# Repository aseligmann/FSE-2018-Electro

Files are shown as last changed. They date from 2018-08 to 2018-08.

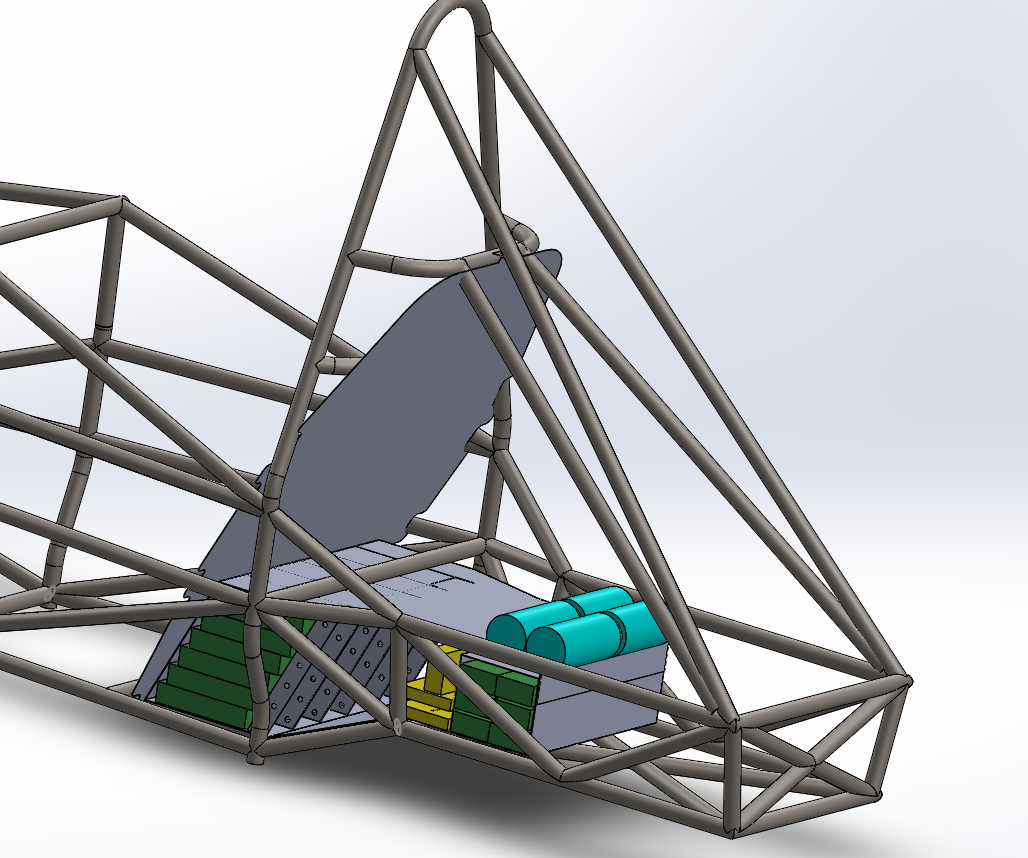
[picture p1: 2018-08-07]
Groups/Battery/Container Design/accumulator position.PNG

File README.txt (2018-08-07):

This archive contains documentation of the most electrical system in Evvee made by Vermilion Racing to participate in the Formula Student UK competition at Silverstone in 2018.
Contents are up to date as of 30/7-2018, unless otherwise noted.

Folder Structure:
	Datasheets
		Datasheets for relevant components and devices used.

	Groups
		Contains description of the work done by each of the electrical subgroups for the 2018 Formula Student race car developed by Vermilion Racing at DTU.
		See groups MasterOS and BMS for most subsystems (BSPD, TSAL etc.).

	Ongoing Sponsorships
		Description of sponsorship deals relevant to the electrical subdepartment.

	Other
		Contains misc. documents which might not be relevant for the future, but can be used as a reference.

	Rules
		Contains the rules for both Formula Student 2018 and FSUK specific rules and guidelines.

	Submitted Documents
		Contains documents relevant for the electrical subdepartment which have been submitted for the FSUK 2018 competition.

Notes:
Autodesk EAGLE has been used for schematics and technical drawings.
Currently the work done by Dominik Mariusz Maszczyk <s163601@student.dtu.dk> is not included. This includes CAN communication, electrical differential and more.

Contact:
Albert Seligmann
Head of Electrical
Vermilion Racing
T: +45 30 30 37 36
E: s163906@student.dtu.dk

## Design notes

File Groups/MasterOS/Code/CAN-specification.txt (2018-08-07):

Pedal/steering wheel position
	Sends signals:
		Normal operation (ID 110, 3 bytes)
			1 byte brake pedal position
			1 byte accelerator position
			1 byte steering wheel position
		Error (ID 10, 2 byte)
			Bit  0: Brake measurement mismatch
			Bit  1: Accelerator measurement mismatch
			Bit  2: Brake overtravel
			Bit  3: Brake undertravel
			Bit  4: Accelerator overtravel
			Bit  5: Accelerator undertravel
			Bit  6: Brake measurement connection failure
			Bit  7: Accelerator measurement connection failure
			Bit  8: Brake pedal short circuit
			Bit  9: Accelerator short circuit
			Bit 10: Steering sensor connection failure
			Bit 11: Steering sensor overtravel
			Bit 12: Steering sensor undertravel
			Bit 13: Steering sensor short circuit

	Receives signals from ID 120:
		Calibration

Audiovisual signaling
	Sends no signals.

	Receives signals from ID 110:
		Normal operation

	Receives signals from ID 10:
		Error

	Receives signals from ID 220:
		Ready to drive

Cooling control
	Sends signals:
		Normal operation (ID 710, 1 byte)
			1 byte cooling control signal

	Receives signals from ID 780:
		Motor status signal

Master
	Sends signals:
		Calibration (ID 120, no message)

		Ready to drive (ID 220, no message)

		Motor status signal (ID 780, 2 byte)
			1 byte motor power
			1 byte motor temperature

	Receives signals from ID 10:
		Error

	Receives signals from ID 110:
		Normal operation

	Receives signals from ID 710:
		Normal operation    ///not anymore

	Receives signals from ID 810:
		Normal operation

	Receives signals from ID 4:
		Error

GLVS BMS
	Sends signals:
		Normal operation (ID 810, 9 byte)
			1 byte temperature sensor 1
			1 byte temperature sensor 2
			1 byte cell1 voltage
			1 byte cell2 voltage
			1 byte cell3 voltage
			1 byte cell4 voltage
			1 byte cell5 voltage
			1 byte cell6 voltage
		Error (ID 4, 9 byte)
			1 byte temperature sensor 1
			1 byte temperature sensor 2
			1 byte cell1 voltage
			1 byte cell2 voltage
			1 byte cell3 voltage
			1 byte cell4 voltage
			1 byte cell5 voltage
			1 byte cell6 voltage

Dashboard
	Receives signals from ID 20, 3 bytes:
		byte 1 (led status)
			Bit  0: Tractive System Indicator
			Bit  1: RTD Indicator
			Bit  2: AMS error Indicator
			Bit  3: IMD error Indicator
		byte 2: Low Voltage Indicator
		Byte 2: High Voltage Indicator

	Sends signals on ID 22, 1 bytes:
		Bit  0: Tractive system activation
		Bit  1: Ready to drive

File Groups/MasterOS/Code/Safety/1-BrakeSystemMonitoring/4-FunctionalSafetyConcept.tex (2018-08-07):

\section{Functional safety concept}
% Reference: DS/ISO 26262-3 section 8
%
% Pre-requisites:
%    - Item definition
%    - Hazard analysis and risk assessment
%    - Safety goals
% 
% Reference: DS/ISO 26262-3 section 8.3.1

\subsection{Pre-existing information}
% The following information can be considered:
%    - Prior architectural assumptions (non-safety related)
%
% Reference: DS/ISO 26262-3 section 8.3.2
The brake monitoring system architecturally consists of the following parts:
\begin{itemize}
\item Brake pedal position sensor
\item Computing system
\item Brake light.
\end{itemize}

\subsection{Derivation of functional safety requirements}
% Functional safety requirements must be specified following DS/ISO 26262-8 section 6.
%
% A functional safety requirement specifies the safety measures and mechanisms that are
% required to comply with the safety goals.
% The functional safety concept is the set of functional safety requirements and the
% architectural elements of the item that they are assigned to.
% The functional safety concept is concerned with:
%    - Fault detection and failure mitigation
%    - Transitioning to a safe state after faults have been detected
%    - Fault tolerance mechanisms, where faults do not lead directly to violation of
%      the safety goals and a safe state is maintained (possibly with degradation)
%    - Fault detection and driver warning to reduce risk exposure time
%    - Arbitration logic to select "worst" fault in case of several simultaneous control
%      requests by different functions
%
% The functional safety requirements are derived from the safety goals and safe states,
% taking into account any prior architectural assumptions.
% One functional safety requirement can be valid for several safety goals.
%
% If a safe state cannot be reached by transition within an acceptable time interval,
% an emergency operation must be specified (e.g. if immediately switching off a system
% would not help, it might help to have it function in a degraded state).
%
% If assumptions are made about the reaction of the driver or other people at risk, the
% assumed actions must be specified in the functional safety concept and the controls
% available to the driver to do this must be specified.
%
% Required information:
%    - At least one functional safety requirement for each safety goal, specified by 
%      considering:
%        - Operating modes of the item
%        - Time interval of fault tolerance, i.e. how long before hazardous event occurs
%        - Safe states of the item (from safety goals)
%        - Emergency operation interval
%        - Functional redundancies (fault tolerance)
%
% Reference: DS/ISO 26262-3 section 8.4.2
\begin{description}
\item [1-FR1-D] To prevent a violation of 1-SG1-D and 1-SG2-D in the event of a light emitting device malfunction, two different systems, employing two different light emitting devices, shall be controlled by the brake system monitoring.
This will immediately lead to a degraded, but safe, state in case of a light emitting device malfunction.
Continuing to drive after transitioning to the degraded state is considered emergency operation, and the malfunction must be corrected as soon as possible.

\item [1-FR2-D] To prevent a violation of 1-SG2-D in the event of a brake light control system malfunction, a safe state shall be maintained by implementing the brake light control system as a normally closed system, so that the brake light will shine when no control signal is detected.
Continuing to drive while no control signal is detected is considered emergency operation, and the malfunction must be corrected as soon as possible.

\item [1-FR3-D] The brake light system and the driver can not detect whether a malfunction has occurred, so to prevent the violation of 1-SG3-D, a bystander will have to alert the driver, who must then bring the car to a stop as soon as possible.
This can be done by e.g. signalling the driver via flags.

\item [1-FR4-D] To prevent a violation of 1-SG4-D in the event of a brake pedal position sensor malfunction, two different systems, employing two different brake pedal position sensors, shall be employed by the brake system monitoring to determine the position of the brake pedal.
If the two systems disagree, the tractive system must be disabled and the driver must be alerted.

\item [1-FR5-D] To prevent a violation of 1-SG4-D in the event of a brake pedal position sensor giving an implausible measurement, the brake pedal position sensors shall be confined to a limited range of operation, and values outside of this range shall send a signal to High Voltage Control to disable the tractive system.
\end{description}

\subsection{Allocation of functional safety requirements}
% Each functional safety requirement shall be allocated to the elements of the prior
% architectural assumptions.
%
% When allocating, the ASIL is inherited from the associated safety goal.
% If several functional safety requirements are allocated to the same architectural
% element, the highest ASIL is inherited unless it can be argued that the safety
% requirements are independent in the architecture.
% 
% If an item consists of more than one system, the functional safety requirements
% for the individual systems and their interfaces shall be specified.
%
% If functional safety requirements are implemented by external measures, the safety
% requirements that are implemented shall be derived and communicated.
% Additionally, the safety requirements of the interfaces with external measures
% shall be specified.
%
% Required information:
%    - Allocation of each functional safety requirement to elements of the architecture
%    - ASIL for development of each functional safety requirement
%    - Functional safety requirements of interfaces to external measures/internal systems
%
% Reference: DS/ISO 26262-3 section 8.4.3
The brake pedal position sensor shall implement the following functional safety requirements:
\begin{itemize}
\item 1-FR4-D.
\end{itemize}
The brake light shall implement the following functional safety requirements:
\begin{itemize}
\item 1-FR1-D
\item 1-FR2-D
\end{itemize}
The team and other bystanders shall implement the following functional safety requirements:
\begin{itemize}
\item 1-FR3-D.
\end{itemize}

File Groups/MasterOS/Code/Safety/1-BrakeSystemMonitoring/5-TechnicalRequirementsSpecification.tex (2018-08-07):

\section{Technical requirements specification}
% Reference: DS/ISO 26262-4 section 6
%
% Pre-requisites:
%    - Functional safety concept
% 
% Reference: DS/ISO 26262-4 section 6.3.1

\subsection{Pre-existing information}
% The following information can be considered:
%    - Safety goals
%    - Functional concept
%    - Prior architectural assumptions
%
% Reference: DS/ISO 26262-4 section 6.3.2
The brake monitoring system architecturally consists of the following parts:
\begin{itemize}
\item Brake pedal position sensor
\item Computing system
\item Brake light.
\end{itemize}

% The technical safety requirements are a refinement of the functional safety
% requirements, taking in account the prior architectural assumptions, and
% turning the item-level functional requirements into system-level technical
% requirements.
%
% The technical safety requirements should be specified considering the following
% properties of the system:
%    - Functional safety requirements
%    - Prior architectural assumptions
%    - External interfaces, e.g. communication and user interfaces
%    - Environmental and functional constraints
%    - (Re)configuration requirements
%    - Dependencies on other systems/elements
%    - Requirements during production, operation, maintenance and repair
%
% If a system should implement functions that are not described by the technical
% safety requirements, a reference should be made to their specifqication.
%
% The technical safety requirements shall specify the response of the system to
% events that affect the achievement of safety goals, including:
%    - Detection, indication and control of faults in the system and communication
%    - Detection, indication and control of faults in external devices/systems
%    - Measures to maintain or transition to a safe state
%    - Measures to implement the warning and degradation concept
%    - Measures to prevent latent (undetected root cause, "random'') faults, e.g. self
%      tests on power up (only for ASILs C and D).
%
% Required information:
%    - Technical safety requirements for the functional safety requirement (see above)
%    - Transitions, fault tolerant time interval, emergency operation interval and
%      measures to maintain state for each safety mechanism that enables a safe state
%    - For safety requirements assigned ASILs C or D, safety mechanisms to prevent
%      latent faults
%
% References:
%    - DS/ISO 26262-4 section 6.1 -- 6.2 and 6.4.1 -- 6.4.5
%
% <<< Repeat this section for each hazardous event >>>
\subsection{1-FR1-D}
This functional safety requirement must be implemented by the brake light system.
This functional safety requirement prescribes that the brake light system must contain two different light emitting devices.

\paragraph{1-TR1-D}
The brake light must be implemented by two electrically parallel light emitting devices, so that the failure of one device does not affect the other.

\subsection{1-FR2-D}
This functional safety requirement must be implemented by the brake light system.
This functional safety requirement prescribes that the brake light control system must be a normally closed system.

\paragraph{1-TR2-D}
The brake light control system must supply power to the brake light when no control signal is detected (i.e. when the control signal is ``floating'').

\subsection{1-FR4-D}
This functional safety requirement shall be implemented by the brake pedal position sensor.
This functional safety requirement prescribes that the brake pedal position sensor shall measure the  brake pedal using two different position sensors, and that the tractive system must be disabled and the driver alerted if the sensors disagree.

\paragraph{1-TR3-D}
The brake pedal position sensor must be implemented by two different position sensors with differing transfer functions.

\paragraph{1-TR4-D}
The two position sensors mentioned in 1-TR3-D must be compared using non-programmable hardware to detect disagreements.
The comparison hardware must be adjustable to compensate for temperature and wear.

\paragraph{1-TR5-D}
If a disagreement between the two position sensors mentioned in 1-TR3-D is detected, a signal must immediately be sent to High Voltage Control to disable the tractive system.

\paragraph{1-TR6-D}
If a disagreement between the two position sensors mentioned in 1-TR3-D is detected, a designated light on the dashboard must be lit to warn the driver.

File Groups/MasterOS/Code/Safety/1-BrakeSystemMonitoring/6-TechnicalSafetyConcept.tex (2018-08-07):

\section{Technical safety concept and system design specification}
% Reference: DS/ISO 26262-4 section 7
%
% Pre-requisites:
%    - Technical safety requirements specification
% 
% Reference: DS/ISO 26262-4 section 7.3.1

\subsection{Pre-existing information}
% The following information can be considered:
%    - Prior architectural assumptions
%    - Functional concept (non-safety related)
%    - Functional safety concept
%
% Reference: DS/ISO 26262-4 section 7.3.2
The brake system monitoring consists of the following overall systems:
\begin{itemize}
\item Brake pedal position sensor
\item Computing system
\item Brake light.
\end{itemize}
\subsubsection{Brake pedal position sensor}
This system consists of the following elements:
\begin{itemize}
\item Position sensors
\item Brake system plausibility device
\item Communication
\end{itemize}

\subsubsection{Computing system}
This system consists of the following elements:
\begin{itemize}
\item Communication
\item Brake pedal overtravel detection
\item Brake position sensor disagreement detection
\end{itemize}

\subsubsection{Brake light}
This system consists of the following elements:
\begin{itemize}
\item Communication
\item Light emitting devices
\end{itemize}

% The technical safety concept is the allocation of the technical safety requirements
% to system elements that are to be implemented by the system design.
% Each element shall inherit the highest ASIL from the technical safety requirements
% that it implements.
%
% The system architectural design implements the functional safety requirements,
% technical safety requirements and non-safety-related requirements.
% When implementing the technical safety requirements, the following shall be 
% considered:
%    - The ability to verify that the system design fulfills the requirements
%    - The technical capability of the design to achieve functional safety
%    - The ability to execute tests during system integration
%    - The allocation and partitioning decisions from the technical safety concept
%
% Required information:
%    - Allocation of technical safety requirements to hardware and/or software elements
%    - Interfaces between system elements and to other systems
%    - Measures for detection, control and mitigation of random hardware failures
%    - Qualitative safety analyses on the system design to identify and eliminate
%      systematic failures and faults
%
% Reference: DS/ISO 26262-4 section 7.4.1 -- 7.4.5
% <<< Repeat this section for each system required to implement the item >>>
\subsection{Position sensors}
This system element shall implement 1-TR3-D.
Therefore, this system element is assigned ASIL D.
It is trivial to verify and test that the element fulfills 1-TR3-D, as it can be easily decided from measurements on the position sensors.

\subsection{Brake pedal overtravel detection}

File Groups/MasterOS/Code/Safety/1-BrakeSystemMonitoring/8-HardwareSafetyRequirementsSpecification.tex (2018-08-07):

\section{Hardware safety requirements specification}
% Reference: DS/ISO 26262-5 section 6.1 -- 6.4.8
%
% Pre-requisites:
%    - Technical safety concept
%    - System design specification
%
% Reference: DS/ISO 26262-5 section 6.3.1

\subsection{Pre-existing information}
% The following information can be considered:
%    - Software safety requirements specification
%
% Reference: DS/ISO 26262-5 section 6.3.2

\subsection{TECHNICAL SAFETY REQUIREMENT NAME}
% Hardware safety requirements shall be derived from each technical safety requirement
% allocated to hardware.
% If a technical safety requirement is allocated to both hardware and software, it should
% be partitioned to yield hardware only safety requirements.
%
% The hardware safety requirements shall include each hardware requirement that relates
% to safety, including:
%    - Safety mechanisms to control internal hardware failures, e.g. a watchdog timer
%    - Safety mechanisms to ensure the element is tolerant to external failures, e.g.
%      an open circuit input to a processor
%    - Safety mechanisms to comply with the safety requirements of other elements
%    - Safety mechanisms to detect and signal internal or external failures
%    - Hardware safety requirements not specifying safety mechanisms, e.g. avoidance
%      of unstable output, requirements for cables and connectors, etc.
%    - Fault tolerant time interval for safety mechanisms from technical safety requirements
%
% The criteria for verification of the hardware design shall be specified, including:
%    - Temperature, vibration, EMI, and other environmental conditions
%    - Supply voltage and other specific operational environment conditions
%    - Component specific requirements
%
% Required information:
%    - Hardware safety requirements for the technical safety requirement
%
% Reference: DS/ISO 26262-5 section 6.4.1 -- 6.4.8
% <<< Repeat this section for each technical safety requirement assigned to hardware >>>

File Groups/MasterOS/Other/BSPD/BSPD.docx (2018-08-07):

# BSPD

Opamps should not get any input voltages higher than Vdd-1.5 which in our case is 10.5V of the 12V.

To secure that the logic gates don’t give out Vdd to the op amps the logic gates Vdd is regulated down to 10.47V.

Break pedals should only operate from 1 to 10V under normal conditions.

Every input and output goes through a fuse to protect the circuit from over current. Every input is checking for short circuit and open circuit with opamps. When an open circuit happens the opamp side is pulled down to ground and thus simulating a short circuit to ground. 0.64V is considered short circuit to ground, 10.43V is considered short circuit for the break pedals. Lem sensor goes from ~0.63V to 3.84V under normal operation. Everything above or below this value is considered short circuit or too high current draw from the battery thus shutting down.

Under normal operation both break pedal sensors will be checked. If one of them goes above a certain voltage e.g. R20/(R20+R1) while current draw is above 40A (2.55V from the lem sensor) The vehicle will shutdown.

To ensure that abnormal behavior is priorities, every short, open and over current, triggers the charge circuit directly. This is ensured by the logic in the circuit. If a error is present for roughly 300ms the vehicle will shutdown. If no error is present the charge circuit discharges through a low resistor and a mosfet.

The output of the circuit goes to LOW when a error is present and thus closes a relay on the shutdown board. So if the output fuse breaks the shutdown circuit will be activated.

R14, R15, R20 and R1 can be changed to change the position where the break pedal sensor triggers the opamp.

R8 and R9, and, R7 and C1, can be used to change the charge time.

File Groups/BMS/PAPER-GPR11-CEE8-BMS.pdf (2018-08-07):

## Battery Safety System for Electric Racing Vehicle

Joakim Vollertzen, s163947 Søren Simonsen, 163907

Department of Electrical Engineering, Technical University of Denmark Course 31015 Introductory project - Electrotechnology

Abstract - The Vermillion racing team is a newly made project on DTU and is working on building an electric race car. The car will be participating the Formula Student Electric competition. More than 100 teams from different universeties will be competing on who can build the best race car. This project is mainly focused on implementing a battery system in the car based on Lithium Polymer technology. When working on batteries, safety is the top priority. The main systems will consist of a BMS to monitor and manage the battery packs. This will be a bought solution, but there is still a lot of research about the batteries required. A power systems board will have to be designed and made. This system will make sure that the battery box will be isolated from the rest of the system in case of a fault or emergency. A seperate system will also be designed and made to indicate the activity status of the battery box. This will have to detect both the outside voltage of the battery pack and the physical state of the relays. This project will be in collaboration with other department spread out on the mechanical and electrical department. All these departments will be under the Vermillion Racing team, and the ultimate goal is to compete and win in the competition.

I. INTRODUCTION

This project is part of a larger project, which goal is to design and build an electric racecar. The car will be entirely designed and build by DTU students and will compete in the Formula Student Electric (FSE) competition at the Silverstone track in England. this project is a part of the Vermillion racing team, which team consist of about 50 DTU students. The Formula Student is a Blue Dot project, and is expected to continue each year from now on. This means that the parts designed and produced in this project will either be optimized or used as inspiration in next years competetion.
This project is focused on the development of a Battery safety system. This system is mainly responsible for monitoring the battery system and disconnecting the battery from the rest of the high voltage system (tractive system) in case a fault is detected in the car. This system will include a Battery Management system (BMS), a Tractive System Active Light (TSAL), and a power systems board.
The battery will be isolated from the rest of the system through a two Accumulator Isolation Relays (AIR). The power systems board will make sure any of the safety systems and shutdown buttons is able to disconnect the relays in case of a fault.
The car will have a large battery container consisting of several lithium-polymer batteries. These kind of batteries contain a large amount of energy that they can discharge very fast. Because of that, it’s very important to handle the batteries in the right way to make sure the car and the people close to it are safe.
Working with the batteries is not easy, and a lot of safety precautions have to be made. It’s important to know exactly which state the batteries are in. If the batteries are not in use, or if an emergency should arise, it’s also important to be able to disconnect the battery box from the rest of the system. There are three main problems which arise when working on a battery system:
1. How can we monitor and manage the battery within safe conditions?
2. How can we make sure that the battery is only connected to the tractive system when it’s safe and desired?
3. How can we indicate the activity status of the tractive system?

II. "PROBLEMS AND RISKS"

Lithium Polymer (LiPo) batteries have a large advantage over other battery technologies as they have a high energy density and discharge rate. This makes it possible for the car to drive further and accelerate faster. The disadvantage is that they are more complicated to operate, and they are more dangerous if a fault should occur.
Different problems can arise when working with LiPo batteries. The battery packs consist of smaller cells, and if their voltage is too low or high, or if the voltages of the cells are not balanced, the battery can destroy itself and in the worst case ignite or explode. This kind of battery have a very high discharge rate and high capacity, if a load draws too much power or if the battery is shorted, it can overheat and ignite or explode. The battery in the car is made out of several smaller packs packed into a box. If the battery box is not operated safely, there is a risk of fire, explosion and/or electrocution. The safety of the battery system is therefore the top priority for this project.
The battery packs will be mounted in a large battery box. To monitor and regulate the battery box, a BMS must be implemented in it. The BMS will constantly measure the voltage of all the cells and make sure they are at a safe level. The total power output of the battery box will also have to be measured to make sure that the connected load won’t draw more current than the batteries can safely provide. Several temperature sensors will be mounted inside the battery box to make sure the batteries are not overheating. To charge the battery, a charger made for the battery setup is necessary. The charger will communicate with the BMS over a CAN bus so the cells can be balanced correctly and so the battery won’t get overcharged.
The battery box will be connected to a pair of motor controllers which controls the motors and decides how much power is used by each motor. These motor controllers have a high capacitance. Because of the high discharge rate of the batteries, a pre-charge system must be implemented to limit the in-rush current to the motor controllers. Otherwise, the relays may weld shut and it wont be possible to open them again. The pre-charge system will charge the motor controllers capacitor banks via a power resistor to limit the current. When the outside system voltage reach at least 90% of the full battery voltage, it is safe to close the main relays. When the battery box is disconnected again after use, the capacitor bank in the motor controllers will still be charged. Therefore, a discharge system will have to be made. The discharge system will dissipate the remaining energy in the motor controllers through an array of power resistors. This should happen in less than 5 seconds to make sure the car is safe after the battery box has been disconnected.
Beside potential battery faults, many other faults and dangers can occur in a race car. These faults can be either electrical errors or accidents. If these faults occur, it can be dangerous to the driver and it can destroy the electrical system. It is therefore important that the battery box is quickly disconnected from the tractive system if a fault or accident should happen.
Some of the faults that can occur are isolation errors, battery errors, crashing and brake errors. The isolation error can be detected by using a device which can measure the low voltage system and the battery box and trigger if an isolation error has occured. We need to make sure that the battery box will be disconnected from the tractive system in case the car is in a crash to limit the risk of short circuits and electrocution. To ensure the car is used correctly, the car should only start when the driver and the team is ready to drive the car. It will therefore be needed to have a master switch which will be used to turn on the tractive system. To make it possible to work on the low voltage system without having to remove the low voltage batteries, a master switch to connect the low voltage battery to the low voltage system is needed. Several emergency shutdown buttons will also be mounted on the inside and outside of the car to make sure any person can disconnect the battery in case of an accident. Because the electrical system will be used in a car, there is a risk of water damage and the car shaking. To protect the electrical components in the car, all components must either be water proof or placed in a water proof container. They will also be mounted securely to the car so they wont shake out of place To indicate that the battery box is completely disabled and all the relays are open, a Tractive System Active Light (TSAL) must be implemented. The TSAL itself can’t affect the electrical system, and is only an indication of the battery box status. Even though the battery box have several safety systems, it’s important to have a seperate system to monitor and indicate the activity status of it. This ensures that a person can see clearly if the car and battery box itself is safe to be around. Because the TSAL is isolated from the rest of the system, a fault is unlikely to affect the function of the indicator.
To ensure that the TSAL always indicate the status of the battery box, it will have to measure the physical state of the main relays (AIRs) and the outside system voltage present on the battery box terminals. It will be measured by nonprogrammable logic which is only powered by the battery. If any of the relays are physically closed or if the outside system voltage exceed 50 V, the TSAL must blink red. If all relays are open and the outside voltage is below 50 V, the TSAL will switch to a constant green ligth.

III. "RESEARCH AND DEVELOPMENT"

The problems and risk mentioned in last section have to be solved so that the car is both safe for use but also compliant with the FSE rules. This means that our solution will be heavely influenced by the rules so that the car can compete in the competetion without any penalty points.
All the faults described in the previous section are used to decide when the car is safe to drive. All these faults will be detected by seperate systems in the car, and when these faults are detected, the AIRs will open and isolate the battery. To make sure that the AIR’s are only activated when desired, the current activating the AIR’s must be directly supplied by the low voltage system and flow directy through the relays, switches and buttons that activate them. This is done so each part of the safety system can directly stop the current from reaching the AIR’s. The safety system will be centered around a power systems board. This board will be a PCB and is where the relays will be placed. These relays will then be closed by their respective safety systems. All these relays, buttons and switches are a part of the low voltage system and use 24V. The power systems board will also have the relays necessary to control the pre-charge and discharge phase along with relays to control the individual AIRs. This is mainly used by the BMS. As the pre-charge and discharge systems are connected directly to the tractive system, they are galvanically isolated from the low voltage system present on the power systems board.

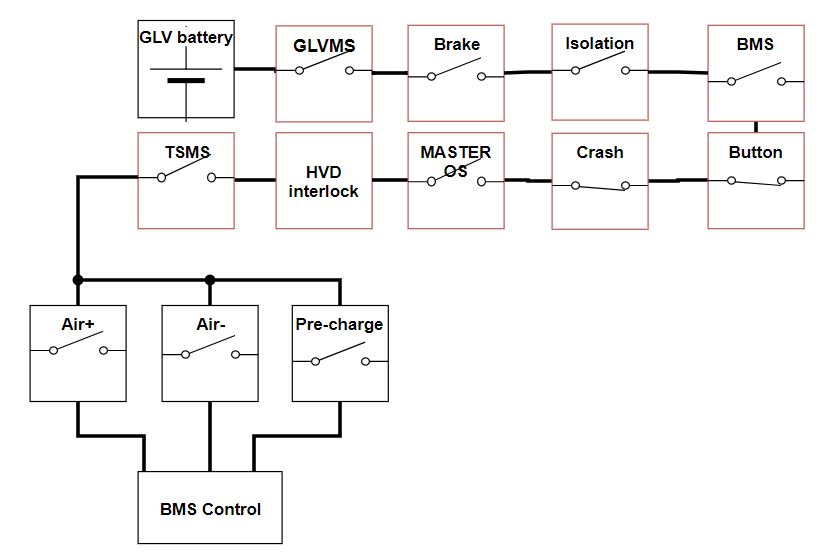
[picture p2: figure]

Fig. 1. Simple block diagram of safety system

Figure 1 shows a blockdiagram of the safety system responsible for opening and controlling the AIR’s. The first block after the low voltage battery is the Ground Low Voltage Master Switch (GLVMS). This switch supplies power to all the systems in the car which use 24V, and is the first swich needed to be turned on in order to start the car. This is a master switch, and it is important that it will not be turned when it is not needed. When the switch is turned off, the handle can be removed and the switch can be locked and tagged. The brake errors consists of two subsystems. The break system plausibility device make sure that the battery is disconnected if the car is accelerating and braking at the same time. This means that the driver can always stop the car if the accelerator is stuck due to either software or hardware fault. The break overtravel switch will disconnect the battery if the break pedal is pushed all the way down. This can happen if the brake fluid is leaking. These are not systems designed in this project, but they will have a relay each on the power systems board.
The isolation error is detected by a BENDER ISOMETER® IR155-3203/IR155-3204. This part is required to be used by the competetion, and makes sure that the battery is always isolated from the low voltage system and the car chassis ground. The relay will have to be latched so the battery is disconnected until the fault is inspected and fixed.
The BMS relay in the safety system is latched in the same way that the iosolation is. Both the Isolation and the BMS need an indicator light on the dashboard of the car, so the driver and the team know where the fault lies. This light needs to be on until the relay on the power systems board has been manually reset. These indicators will be controlled directly by the cars master controller.
Three emergency shutdown buttons will be located on the car. One in the cockpit and one on each side of the car. According to the rules of FSE, these buttons must either be push-pull or push-rotate, and all three buttons must be able to disconnect the current flow to the AIR’s directly.
The crash sensor is a 360 degrees sensor which detects impact load. When an impact load between 6g and 11g is detected, it opens the safety system. The crash sensor can be reset by pushing a button on the device.
The master controller will also have a relay on the power systems board, and in therefore able to connect and disconnect the battery when starting and stopping the car. It is therefore also able to disconnect the battery in case of a fault.
The next box in figure 1 is the High Voltage Disconnect. It works by opening the safety system when the cable connecting the battery box and the motor controller is disconnected. This is done through a interlock.
The Tractive System Master Switch (TSMS) is the last link in the chain. This is a physical switch identical to the low voltage master switch, and is used to turn on the tractive system.
The tractive system can be activated when none of the parts of the safety system have detected a fault, all of the switches and buttons are closed and the driver has entered the ready to drive mode using the master controller. The relays controlled by the BMS are used to control the pre-charge sequence. After a engine start is requested, the master controller will request the BMS to run the pre-charge operation.
The discharge relay is controlled by the same signal going from the tractive system master switch to the AIR’s. The relay is normally closed, which means that the discharge phase will run automatically when the battery is disconnected. All signals which control whether the AIR’s are opened og closed are system critical. This means that they must be protected agains short circuit and open circuit. If a signal wire is broken, the relay it’s connected to will automatically open. If a short circuit of the signal wire is present, a fuse will blow and the relay will open. Therefore, all signals will go to a safe state if there is open circuit or short circuit.
In the beginning of the project, the battery setup was already set to a voltage between 80-120 V. The BMS was chosen to be a LiBAL N-BMS as Lithium Balance would like to sponsor it. The system is very flexible and can work with several battery configurations. Because of that, most of the work was already done with the BMS.
In 2, a simple block diagram of the battery system can be seen. The BMS consist of a master board with three slave boards connected to it. The battery systems is made of 7 battery segments in series each consisting of 6 battery packs in parallel. Each segment will have 4 temperature sensors and 4 cells which voltages are monitored by a slave module. The slave boards are able to measure the voltage of the cells and balance them through on-board resistors. The battery temperature can also be measured in several different locations using external sensors. The master board is measuring the total battery voltage along with the cell voltages and controlling the charging and balancing of the cells. Through a hall-effect current sensor, the current through the battery is measured to ensure the safety threshold is not exceeded. Using three external relays located on the power systems board, the BMS master is able to close the two AIR’s and the pre-charge relay to control the pre-charge operation safely.
The rules specified that a third of the cells must have a temperature sensor mounted at the negative pole. This was problematic for both the BMS and the battery box itself. All the temperature sensors would cause space problems in the pack because of the cables, and the BMS would not be able to monitor all the sensors without getting extra slaves for it. In collaboration with our advisor, Nenad Mijatovic, and the battery group, Albert Segilmann and Frederik Højlund, a solution was found where one sensor could measure the temperature of two cells. This made it possible to fit the whole battery system in a small closed container.
The TSAL was complicated to make because of the high safety factor and many rules. It was not allowed to measure the control signals to the main signals, and must do it by directly measuring on the relay terminals. This was to make sure the TSAL measures the right state in the event that the relays got stuck or welded shut. It was also necessary to power the TSAL with the high voltage battery and not the smaller external low voltage battery. This was to make sure the TSAL would always be powered on when the battery was connected. In 3, a simple block diagram of the TSAL can be seen.

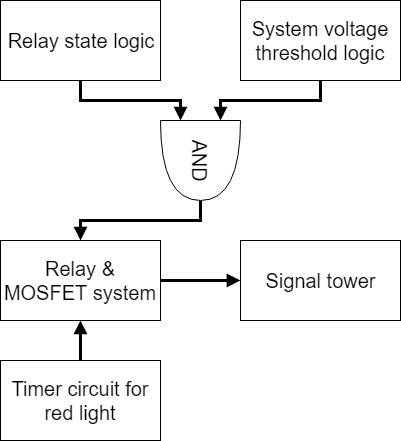
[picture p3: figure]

Fig. 3. Simple block diagram of Tractive System Active Light (TSAL)

To make sure the system will not indicate a safe state if an unknown input occur or if the trigger circuit breaks, the default state of the circuit is set to indicate an active battery. This is done via switch relays which will have the normal position blink the red light. Two independent circuits will have to both indicate a safe state, represented as the AND-gate, for the light to switch green and indicate a deactivated battery. In reality, two transistors and a relay will be in series acting like an AND-gate.
The Relay state logic will determine the state of the two main relays through a resistor. The output of the resistor network will be compared to a reference signal via two op-amps. The measured signal and reference signal is both referenced to the supply voltage, thus making it possible to work with the large range of supply voltages which occur depending on the battery charge level. Each op-amp will trigger a transistor, and if both op-amps are triggered, both relays will be open and indicate a safe state.
The system voltage threshold logic will independently measure the voltage over the battery terminals on the outside of the battery box. If the threshold of 50V is reached, an op-amp will open a relay and indicate an unsafe state. If the circuit is below 50V or completely unpowered, which will be the case if one or both of the relays are closed, the relay will close again and indicate a safe state.
If both circuits indicate a safe state, the light will switch to a constant green via switch relays. If that is not the case, the circuit will blink the red light via the timer circuit. If the circuit lose a connection to the batteries, it would not be able to determine the relay state and battery voltage. But because it’s powered by the battery, the TSAL will be unlit, and therefore indicate an error and potential unsafe state.

IV. PRODUCTION AND TESTING

The power systems board will be a PCB. This PCB mainly consists of relays and connecotors to the varius parts of the safety system. The power systems board will have both low voltage and high voltage systems. These needs to be proberly isolated from each other, which is done by placing each system at least 20 mm from each other on the PCB. The low voltage and high voltage is placed on the same PCB to save space and make a more simple system. When the power systems board has been completed, it will be placed in a closed box with waterproof connectors.
To make sure that the power systems board works properly, the board needs to be tested. The first test is to make sure all the relays and buttons work as designed. The buttons and switches will be directly connected to the power systems board, and the signals from the active systems will be emulated with a power supply.
A Arduino will be connected to an array of relays. These relays will be connected to a variable power supply to emulate different signal voltages. The Arduino can be programmed to test the relays on the board in different state configurations. By changing the voltage on the power supply, a large range of signal voltages can be tested to make sure that the system can will still work over a larger range of input signals. This is good to know in case some of the systems can’t supply a steady signal voltage.
It is important to test all possible connections on the board with a multimeter while activating the relays. This is done to test if the board is printed and designed proberly. If this test is succesfull, it would confirm that the design of the power systems board works correctly. This test will be done using the equipment in X-lap.
The second test is a test to make sure the pre-charge and the discharge relays works properly. This will be done by connecting a capacitor to emulate the motor controller. A power supply will be connected to emulate the battery box. During the test, the temperature of the resistors will be monitored to make sure they aren’t overheating.
Before mounting the batteries in the container, the BMS and all battery-related systems must be tested and approved. The test setup will be close to the one illustrated in 2, but with a few modifications. The first tests will consist of one master and two battery packs, keeping the voltage at a minimum while still being able to configure and test the BMS functionality. If the test is successful, more batteries can be added in series until the full system voltage is reached using all three slaves. The load will be in the form of an adjustable load able to dissipate all the heat, but it will only be connected after the BMS is fully configured and working. This should be connected in combination of the main relays and power systems board to test if they can safely disconnect the battery. If anything unexpected should occur under testing, this will also be used to isolate the batteries and prevent an accident. The charger we’re using will also be testet, where it’s important to check if the CAN communication between BMS and charger is working. The BMS is also checked to see if the cells are balanced and charged to the correct voltage. If there is time en resources available, it will also be possible to tweak the PID parameters of the charging operation to keep the charging time to a minimum. But this will have to be monitored closely as a underdamped PID regulation could

overcharge the batteries.
It’s important to also test the batteries in combination with the rest of the system. The relays and power systems board should be tested first, but the TSAL can also be tested easily when all the batteries in series is connected together to reach the full system voltage. Afterwards, the system will have to be implemented in the battery box where temperature tests are especially important. If the cooling in the box isn’t suffucient, the batteries can overheat in the closed container and ignite.
The TSAL will be made out of simple electronic components and soldered onto a PCB. The PCB will be fit in a waterproof box which is easy to install on the car later on. In the testing phase, a milled prototype PCB will be used. This is cheap to make and fast to mill if a correction have to be made.
To test the relay state logic, a 30V power supply is enough to power the logic and the light. A small relay will be used to emulate the function of the main relays. The four possible states of the two relays is tested, where it is expected for the light to stay red until both relays are open.
To test the system voltage threshold logic, a supply of 60V is required. While the two relays are open, the supply is increased until around 50V where the light is expected to trigger. This will also be tested with the other possible relay state combinations to make sure that the two circuits work together.
If both tests are successful, the circuit will have to be tested at the full 120 V to make sure the regulators work at higher voltages without overheating. At last, the TSAL will be tested with the full battery setup including the two main relays and the pre-charge relay. Afterwards, the TSAL can be implemented in the car.
V. CONCLUSION

Through this project, we have learned a lot about how to design and build a safe electrical battery system for a car. We have focused on what to do to protect and regulate the battery, and when to disconnect the battery from the rest of the cars electrical system.
A BMS system have been designed to monitor and regulate the batteries. The system have not been implemented yet due to delay in the BMS delivery, but the battery setup have been designed along with the tests required to make sure the BMS is working as expected.
A power systems board have been designed and the first prototype is close to be ready for testing. It is expected to go into testing shortly after the project is done. Based on the test, the design will be improved and in the end send to production at a professional PCB manufacturer.
The first design of the Tractive System Active Light have been tested, where it successfully measured when the outside system voltage reached a threshold of 50 V. The part of the circuit to check the physical state of the main relays did not pass the test, but a new design have been made and a new prototype is close to being made. This circuit will also be manufactured by a professional PCB manufacturer when it is fully tested and approved.
Overall, we are pleased with the progress we made throughout the project. we unfortunately didn’t implement all the systems, but we learned a lot about working on larger projects and collaborating with other departments.

ACKNOWLEDGEMENT

Thanks to Nedad for guiding and helping us during the project. Thanks to Esben and Bjarni for helping us with PowerLab introduction and access. Thanks to the Vermillion racing team for letting us be apart of this project. Thanks to the sponsors who made this project possible, especially Lithium Balance for giving us a course on how to use the BMS and thanks to Tonny from PowerLab for helping us milling PCB’s.

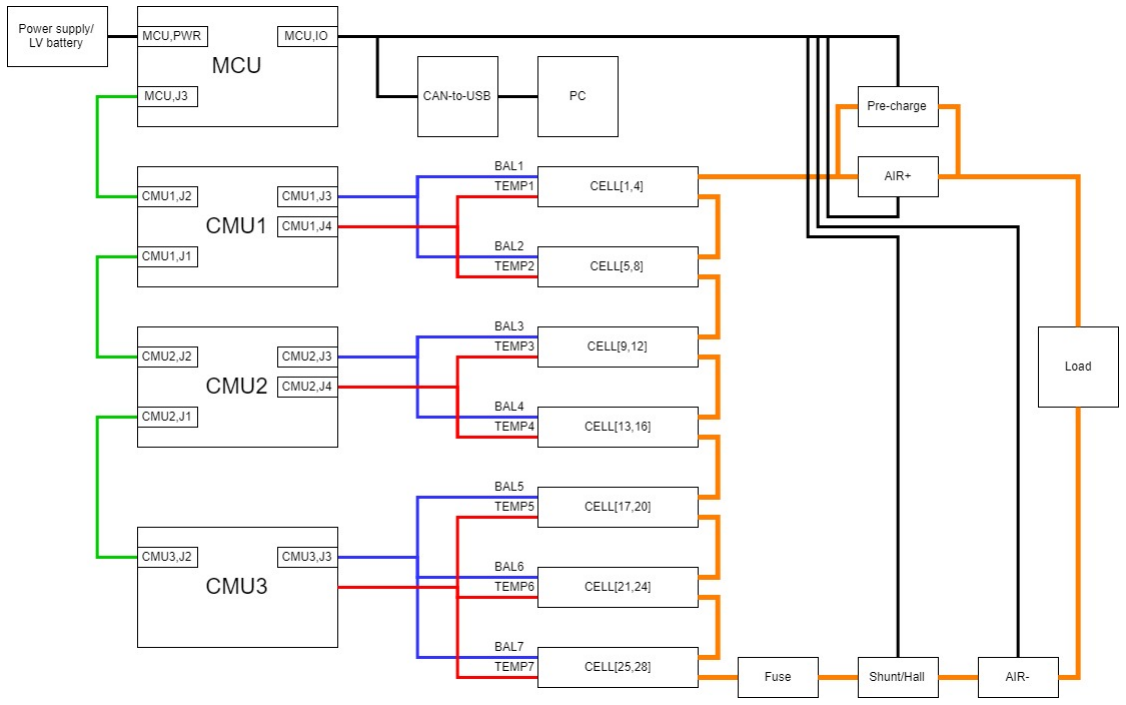
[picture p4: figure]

Fig. 2. Diagram of the battery system

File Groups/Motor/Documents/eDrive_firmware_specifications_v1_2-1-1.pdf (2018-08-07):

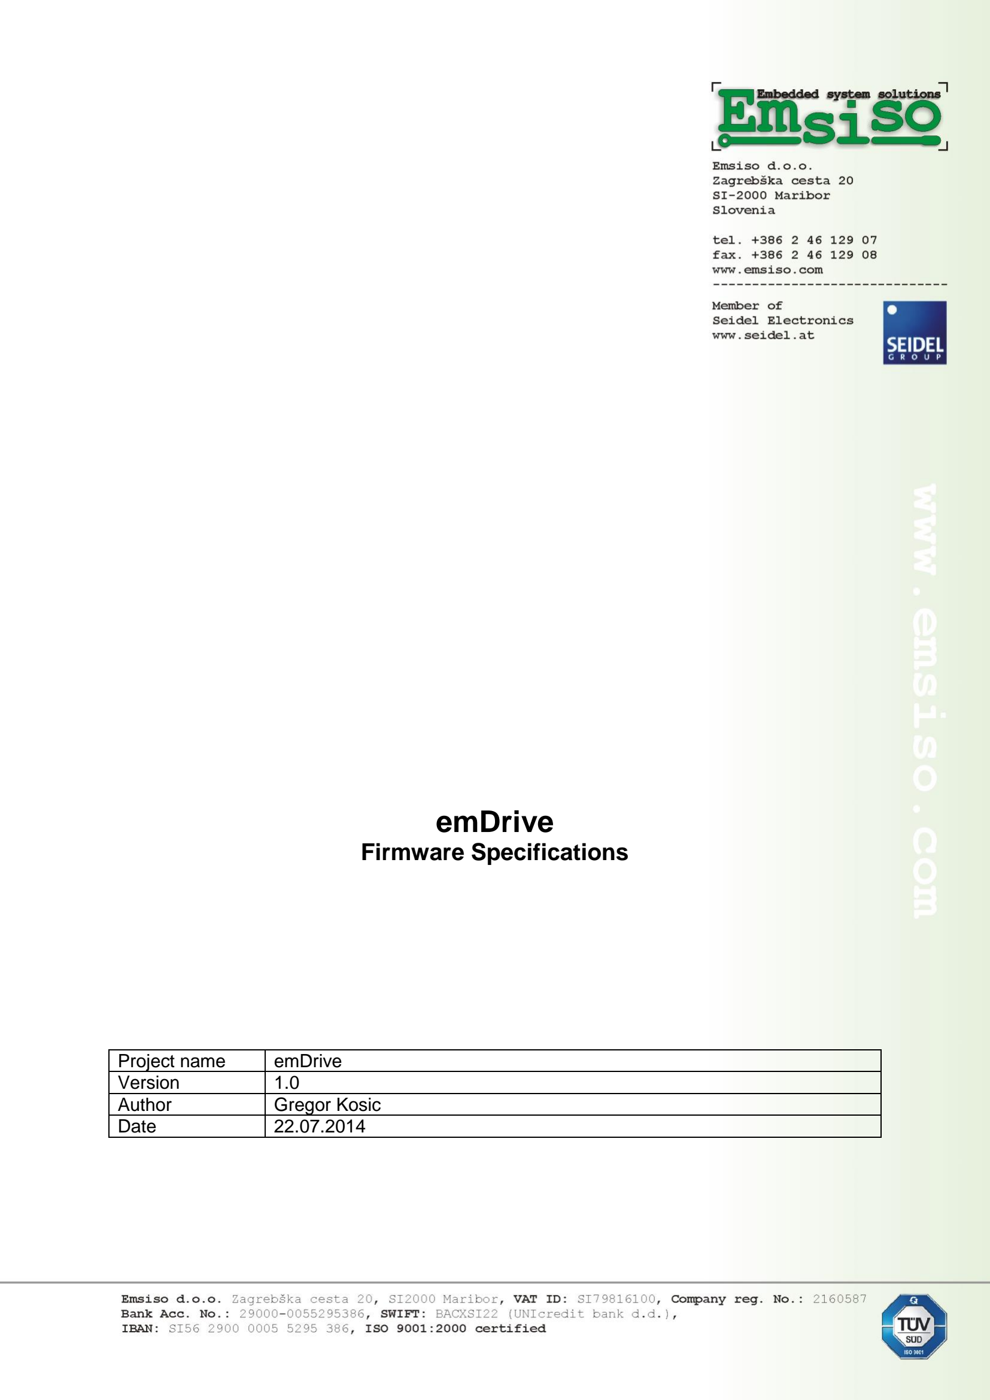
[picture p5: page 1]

## emDrive

### Firmware Specifications

Project name | emDrive
Version | 1.0
Author | Gregor Kosic
Date | 22.07.2014

emDrive Firmware Specification

## History

Version | Author | Description | Date
1.0 | Gregor Kosic | Initial document creation | 22.07.2014

## Table of contents

TABLE OF FIGURES

### 1 INTRODUCTION

### 1.1 General Information

This documentation “Firmware description” provides the firmware details of the emDrive150 controller. It contains detailed description of architecture, device states, operation modes, error handling and object dictionary.

EmDrive family are advanced BLDC motor controllers for e-drive systems. Drives are designed to power brushless and induction motos, it supports standard three hall sensor with 60 and 120 degree configuration, absolute digital SSI encoder with RS422 interface, resolver, 5V analogue sin/cos, and encoder. Due the vector current control, torque ripple and vibrations in motor, there is no audible noise. Integrated current, velocity and position current control functionality allows accurate sophisticated positioning applications.

emDrives are specially designed to be controlled over CANopen network as a slave node and additionally can be operated through any RS232 communication port and local control.

### 1.2 Operating Principles

The CiD DSP 402 CANopen Device Profile for Drives and Motion Control is used to provide drives in a CAN network with an understandable and consistent behavior. The profile is built on top of a CAN communication profile, called CANopen, which describes the basic communication mechanisms common to all devices in the CAN network.

The purpose of the drive units is to connect axle controllers or other motion control products to the CAN bus. They usually receive configuration information via service data objects for I/O configuration, limit parameter for scaling, or application-specific parameters. At run time, data can be obtained from the drive unit via CAN bus either by polling or in event-driven mode (with properly-mapped TPDOs).

The motion control products use process-data object mapping for real-time operation, which may be configured using service data objects (SDOs). This communication channel is used to interchange real-time data-like set-points or actual values such as position actual values.

The most important part of a device profile is the object dictionary description. The object dictionary is essentially a grouping of objects accessible via the network in an ordered pre-defined fashion. The DSP 402 standard objects of single-axis drives, like the
Harmonica, are all in the index range of 0x6000 to 0x67ff.

GENERAL NOTICE:
For latest version of this document please contact the e-mail address info@emsiso.com

### 2 SYSTEM OVERVIEW

### 3.1 Device Architecture

CAN Communication interface of the emDrive BLDC controller follows the CiA CANopen specifications:
Support of all CiA 301 services
Compliant to CiA-301 V4.2
LED CiA-303

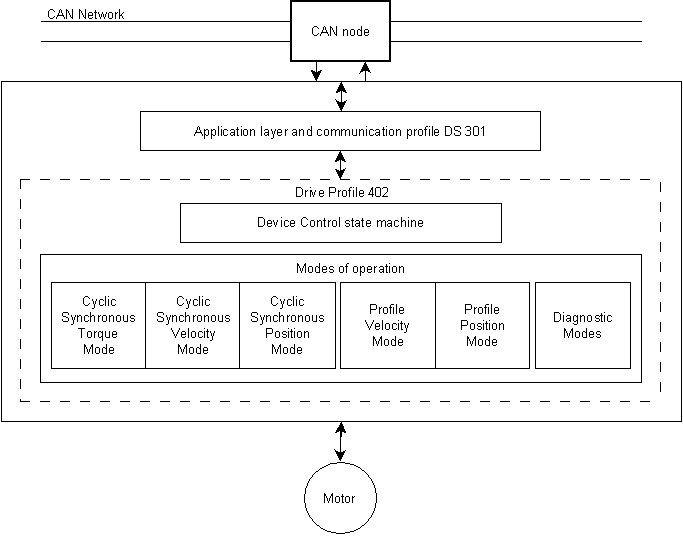
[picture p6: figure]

Figure 2-1: Communication architecture

Device Control
Drive managing and mode-specific command are executed by the state machine.

Modes of operation
Mode of operation is defining the behavior of the drive.

### 3.2 Device Control

Figure 2-2 contains detailed description of the device states and all possible controlling sequences for operating the emDrive.

Also states of the drives are determining which commands are accepted.

States may be changed using the Controlword and/or according to internal events. The current state can be read using the Statusword.

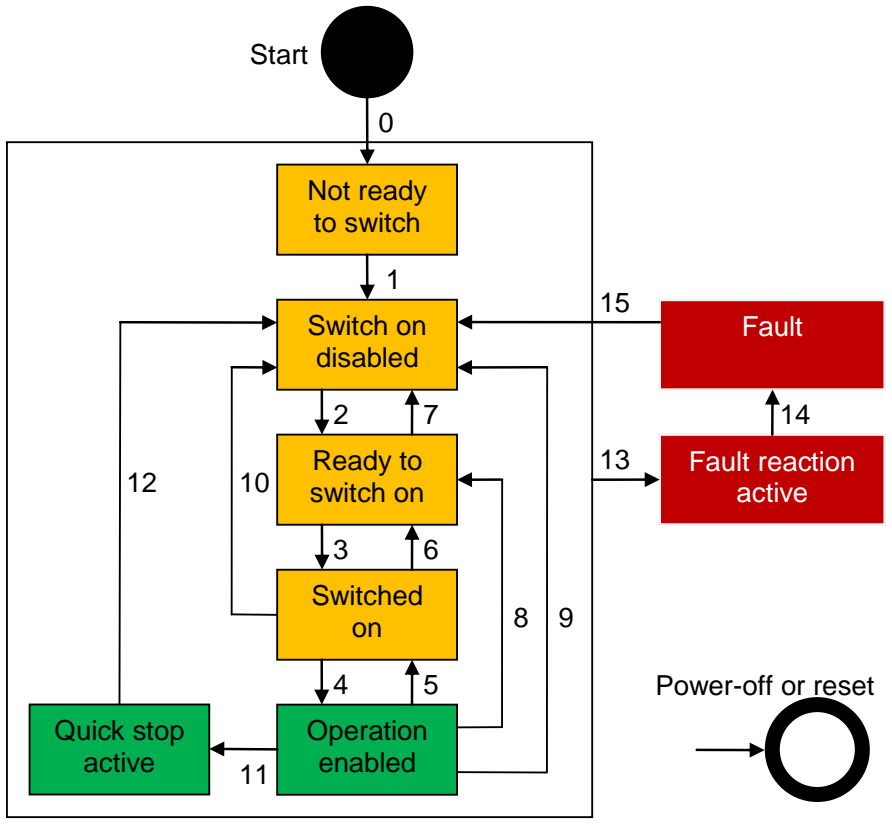
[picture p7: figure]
Not ready to switch; Switch on disabled; Ready to switch on; Switched on; Operation enabled; Quick stop active; Fault reaction active; Fault; Start; Power-off or reset

Figure 2-2: Device State Machine Block Diagram

3.2.1 State Transitions
State transitions are caused by internal events in the device or by command from host via the Controlword.

If command is received which causes a change of state, this command will be processed completely and the new state attained before the next command can be processed.

Table 2-1: Transition events and actions
Transition | Event(s) | Action(s)
0 | Automatic transition after power-on or reset | Initialize drive, enable breaks, start local control if enabled
1 | Automatic transition | Start safety procedure, disable drive function, initialize feedback, internal set-points cleared
2 | “Shutdown” command from control device or local signal received | Disable drive function
3 | “Switch on” command received from control device or local signal | Disable breaks
4 | “Enable operation” command received from control device or local signal | Enable drive function
5 | “Disable operation” command received from control device or local signal | Drive function disabled, disable breaks
6 | “Shutdown” command received from control device or local signal | Drive functions disabled, enable breaks
7 | “Quick stop” or “disable voltage” command received from control device or local signal | Drive functions disabled, enable breaks, initialize feedback, internal set-points cleared
8 | “Shutdown” command received from control device or local signal | Drive functions disabled, enable breaks
9 | “Disable voltage” command received from control device or local signal | Drive functions disabled, enable breaks, initialize feedback, internal set-points cleared
10 | “Disable voltage” or “quick stop” command received from control device or local signal | Drive functions disabled, enable breaks, initialize feedback, internal set-points cleared
11 | “Quick stop” command received from control device or local signal | none
12 | Automatic transition | Disable drive function, initialize feedback, internal set-points cleared
13 | Fault signal | None
14 | Automatic transition | Disable drive function, enable break
15 | “Fault reset” command received from control device or local signal | Clear fault condition if no fault is present

3.2.2 Device Control Commands
Device control commands are executed by writing in the Controlword, codes given in Table 2-2

Table 2-2: Command coding
Command | Bit of the Controlword | Transitions Bit 7 | Bit 3 | Bit 2 | Bit 1 | Bit 0
Shutdown | 0 | X | 1 | 1 | 0 | 2, 6, 8
Switch on | 0 | 0 | 1 | 1 | 1 | 3
Switch on + enable operation | 0 | 1 | 1 | 1 | 1 | 3+4 (NOTE 1)
Disable voltage | 0 | X | X | 0 | X | 7, 9, 10, 12
Quick stop | 0 | X | 0 | 1 | X | 7, 10, 11
Disable operation | 0 | 0 | 1 | 1 | 1 | 5
Enable operation | 0 | 1 | 1 | 1 | 1 | 4
Fault reset | From 0 to 1 (NOTE 2) | X | X | X | X | 15

NOTE 1: Automatic transition to enable operation state after executing SWITCHED ON state functionality.
NOTE 2: Bit 7 transition from 0 to 1

### 4 ERROR CODES AND ERROR BEHAVIOR

### 4.1 Emergency Message Frame

When device-internal failure is detected emDrive will transmit emergency message frames over the CANopen with highest priority. Message frame shown in Table 4-1.
An emergency message frame will be transmitted only once per error event and consists of the Error Code and the actual Error Register.

Table 4-1: Emergency message frame
Byte | 0 | 1 | 2 | 3 | 4 | 5 | 6 | 7
Content | Emergency error code | | Error register | Not used (always “0”)

emDrive can detect several variety of device error. The reaction to an error depends on error type. After execution of the fault reaction, the device changes to fault state and the drive will be disabled.

### 4.2 Device Emergency Error Codes

4.2.1 | 0x1000 Generic error
Error Code | 0x1000
Cause | Unspecific error occurred
Effect | device disabled red error led “on” error flag set in Statusword (bit 3)
Error Recovery | Reset fault with Controlword
4.2.2 | 0x2220 Overcurrent error
Error Code | 0x2220
Cause | short circuit in motor winding controller gain to high (Current control parameters, Velocity control parameters) power stage damaged
Effect | device disabled red error led “on” error flag set in Statusword (bit 3)
Error Recovery | Reset fault with Controlword
4.2.3 | 0x3210 DC link over voltage
Error Code | 0x3210
Cause | Power supply voltage to high
Effect | device disabled red error led “on” error flag set in Statusword (bit 3)
Error Recovery | Reset fault with Controlword

4.2.4 | 0xFF01 Phase A current measurement
Error Code | 0xFF01
Cause | Current phase A hall sensor missing or damaged
Effect | device disabled red error led “on” error flag set in Statusword (bit 3)
Error Recovery | Reset fault with Controlword
4.2.5 | 0xFF02 Phase B current measurement
Error Code | 0xFF02
Cause | Current phase A hall sensor missing or damaged
Effect | device disabled red error led “on” error flag set in Statusword (bit 3)
Error Recovery | Reset fault with Controlword
4.2.6 | 0xFF03 High side Fet short circuit
Error Code | 0xFF03
Cause | DC voltage not applied to bridge or to low motor phases not connected to controller internal low side fet error circuit damaged damaged high side fets
Effect | device disabled red error led “on” error flag set in Statusword (bit 3)
Error Recovery | Reset fault with Controlword
4.2.7 | 0xFF04 Low side Fet short circuit
Error Code | 0xFF04
Cause | DC voltage not applied to bridge or to low motor phases not connected to controller damaged low side fets
Effect | device disabled red error led “on” error flag set in Statusword (bit 3)
Error Recovery | Reset fault with Controlword
4.2.8 | 0xFF05 Low side Fet phase 1 short circuit
Error Code | 0xFF05
Cause | motor phases not connected damaged low side fets on phase 1
Effect | device disabled red error led “on” error flag set in Statusword (bit 3)
Error Recovery | Reset fault with Controlword
4.2.9 | 0xFF06 Low side Fet phase 2 short circuit
Error Code | 0xFF06
Cause | motor phases not connected damaged low side fets on phase 2

Effect | device disabled red error led “on” error flag set in Statusword (bit 3)
Error Recovery | Reset fault with Controlword

4.2.10 0xFF07 Low side Fet phase 3 short circuit
Error Code | 0xFF07
Cause | motor phases not connected damaged low side fets on phase 3
Effect | device disabled red error led “on” error flag set in Statusword (bit 3)
Error Recovery | Reset fault with Controlword

4.2.11 0xFF08 High side Fet phase 1 short circuit
Error Code | 0xFF08
Cause | motor phases not connected damaged low side fets on phase 1
Effect | device disabled red error led “on” error flag set in Statusword (bit 3)
Error Recovery | Reset fault with Controlword

4.2.12 0xFF09 High side Fet phase 2 short circuit
Error Code | 0xFF09
Cause | motor phases not connected damaged low side fets on phase 2
Effect | device disabled red error led “on” error flag set in Statusword (bit 3)
Error Recovery | Reset fault with Controlword

4.2.13 0xFF0A High side Fet phase 3 short circuit
Error Code | 0xFF0A
Cause | motor phases not connected damaged low side fets on phase 3
Effect | device disabled red error led “on” error flag set in Statusword (bit 3)
Error Recovery | Reset fault with Controlword

4.2.14 0xFF0B Motor Feedback
Error Code | 0xFF0C
Cause | Wrong feedback selected (check feedback type) Feedback damaged or not connected
Effect | - device disabled - red error led “on” - error flag set in Statusword (bit 3)
Error Recovery | Reset fault with Controlword

4.2.15 0xFF0C DC link undervoltage
Error Code | 0xFF0C

Cause | DC voltage not applied to bridge or to low
Effect | - device disabled - red error led “on” - error flag set in Statusword (bit 3)
Error Recovery | Reset fault with Controlword

4.2.16 0xFF0D Puls mode finished
Error Code | 0xFF0D
Cause | Puls mode finished It’s used for fine adjustments and troubleshooting
Effect | - device disabled - red error led “on”
Error Recovery | Reset fault with Controlword

4.2.17 0xFF0E Emergency button pressed
Error Code | 0xFF0E
Cause | Emergency button pressed. If not used pin must be connected to GND
Effect | - device disabled - red error led “on”
Error Recovery | Reset fault with Controlword

### 5 MODES OF OPERATION

0x6060: Modes of operation 0x6061: Modes of operation display

### 5.1 Functional Description

The drive behavior depends on the activated modes of operation. Different modes can be implemented, although not in parallel. Therefore, the user must activate the required function by selecting modes of operation, through the object Modes of Operation and it’s by default set to “no mode” (value – 0). Modes can be set in any state excluding OPERATION ENABLED in this state switching between modes of operation is not recommended. Actual modes of operation is displayed in Modes of Operation Display.

5.1.1 | 0x6060: Modes of operation Object description:
Index | 0x6060
Name | Modes of Operation
Data type | INTEGER8
Saved in EEPROM | Yes

Entry description:
Access | Read / write
PDO mapping | Allowed
Value range | INTEGER8
Default value | 0

Data description:
Value | Description
-128…-6 | Reserved
-5 | Induction VF – testing purposes only
-4 | Aligning rotor position
-3 | Current stepper – testing purposes only
-2 | Voltage stepper – testing purposes only
-1 | Voltage constant angle – testing purposes only
0 | No mode
1…7 | Reserved
8 | Cyclic sync position
9 | Cyclic sync velocity
10 | Cyclic sync torque
11...127 | Reserved
- A read of this object shows only the new value of modes of operation. The actual mode of the drive is reflected in the modes of operation display (0x6061). It may be changed by writing to modes of operation.
- An attempt to access an unsupported mode causes the modes operation set to no mode.

5.1.2 0x6061 Modes of operation display
This object shows the current mode of operation. The meaning of the returned value corresponds to modes of operation option code (0x6060).
| Object description:
Index | 0x6061
Name | Modes of Operation display
Data type | INTEGER8
Saved in EEPROM | No

Entry description:
Access | Read only
PDO mapping | Not allowed
Value range | INTEGER8
Default value | 0

Data description:
Similar to object 0x6060, modes of operation.

5.1.2.1 Induction VF

Induction VF mode uses Test Mode Command (0x2031) to command the Phase Voltage calculation function. For enabling Induction VF mode Test Stepper Enable (0x2040,10) must be set.
In this mode NO protections and limits are active. Proposed use only for developers.

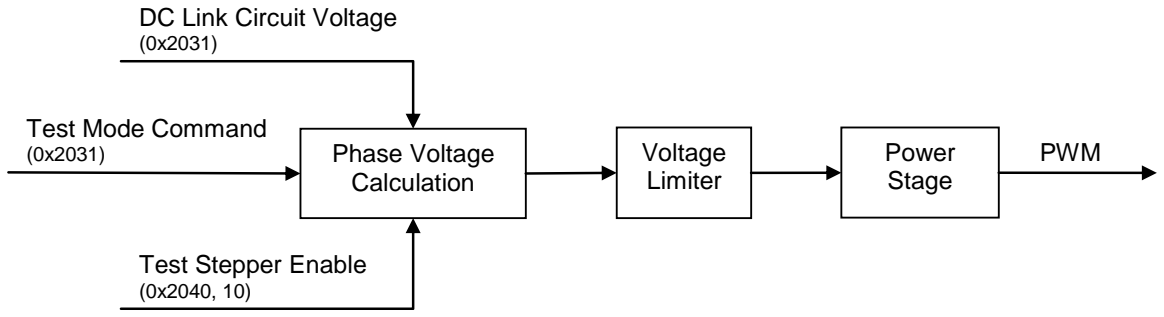
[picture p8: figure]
Phase Voltage Calculation; Test Stepper Enable (0x2040, 10); Test Mode Command; Voltage; Limiter; Power Stage; PWM; DC Link Circuit Voltage (0x2031)

Figure 0-1 Induction VF – Block Diagram

5.1.2.2 Aligning Rotor Position

Aligning Rotor Position is used for determination of rotor position offset. Motor must be able to free spin.
Minimal requested settings for proper determination must be set:
- Motor Type (0x2034),
- Motor Rated Current (0x6075),
- Motor Pole Pairs (0x2033),
- Feedback type (0x2040, 1),
- Feedback Resolution (0x2040, 7),
- Auto aligning rotor position current (0x2040, 11).

Internal state machine is started as soon as proper Modes of Operation (0x6060) is selected and NMT state is changed to operational.
Motor will spin with 20 RPM in both directions for few seconds and calculate rotor position offset. If the procedure will be successful, Motor Phase Offset (0x2040, 3) and Feedback Diretion (0x2040, 4) will be set, drive will go into preoperation mode. Modes of Operation (0x6060) will be set to 0 (No Mode).
In case that procedure will fail, drive will go into Fail State. In Error Register (0x1001) error code 0xFF0B (Error Motor Feedback) will be displayed.

5.1.2.3 Current Stepper

Current stepper mode uses Test Mode Command (0x2031) to command the current stepper control function. For enabling stepper, Test Stepper Enable (0x2040, 10) and Test stepper Frequency (0x2040, 5) must be set.
In this mode only maximum controller current limit is active, other protections and limits are inactive. Proposed use only for developers.

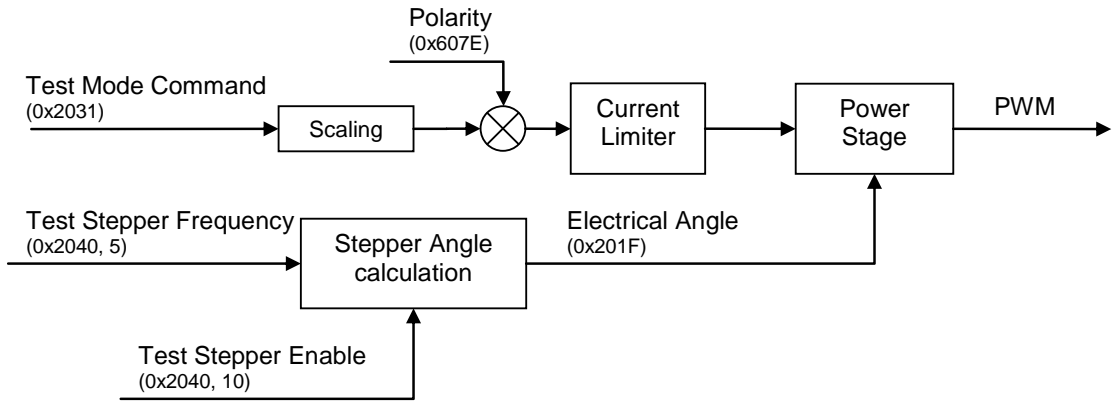
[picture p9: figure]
Scaling; Power Stage; PWM; Electrical Angle (0x201F); Test Stepper Frequency; Stepper Angle; calculation; Test Stepper Enable (0x2040, 10); Polarity (0x607E); Current Limiter; Test Mode Command (0x2031)

Figure 0-2 Current Stepper – Block Diagram

5.1.2.4 Voltage Stepper

Voltage stepper mode uses Test Mode Command (0x2031) to command the voltage stepper control function. For enabling stepper, Test Stepper Enable (0x2040, 10) and Test stepper Frequency (0x2040, 5) must be set.
In this mode NO protections and limits are active. Proposed use only for developers.

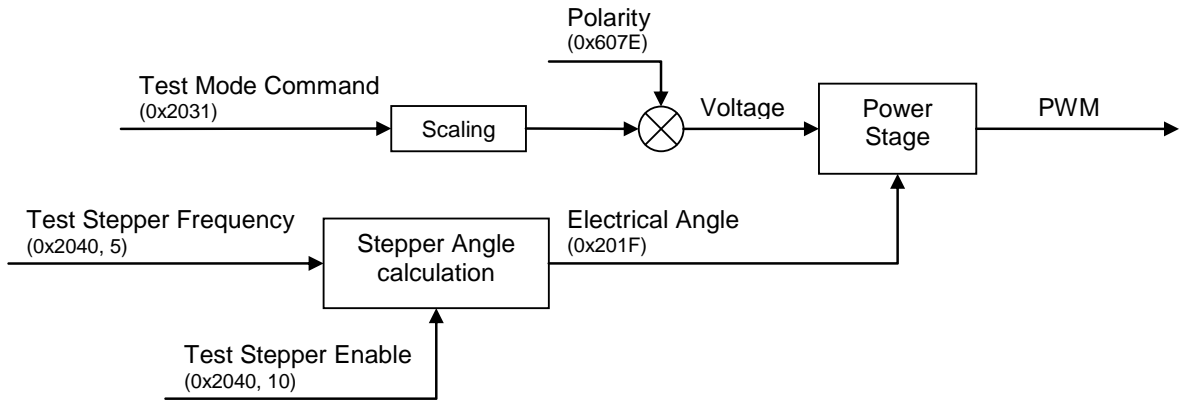
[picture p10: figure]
Test Mode Command (0x2031); Scaling; Polarity (0x607E); Power Stage; Test Stepper Frequency; Stepper Angle; calculation; Test Stepper Enable (0x2040, 10); PWM; Electrical Angle (0x201F); Voltage

Figure 0-3 Voltage Stepper – Block Diagram

5.1.2.5 Cyclic Sync Torque

Cyclic Sync Torque mode uses Target Torque (0x6071) to command the current control function. Find description for block “Limiter” in paragraph 5.1.3 Output current Limitation.
Optionally local control can be enabled and an analog input can be used to command the current control function.

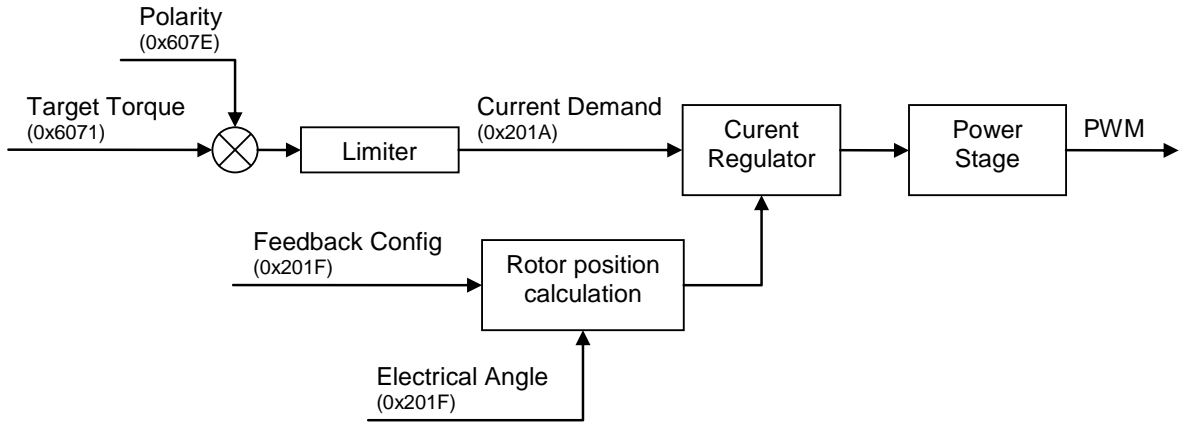
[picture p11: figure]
Target Torque (0x6071); Polarity (0x607E); Limiter; Current Demand; Curent; Regulator; Electrical Angle (0x201F); Feedback Config; Rotor position; calculation; Power Stage; PWM

Figure 0-4 Cyclic Sync Torque – Block Diagram

5.1.2.6 Cyclic Sync Velocity

Cyclic Sync Velocity mode uses Target Velocity (0x60FF) to command the velocity control function.
Find description for block “Limiter” in paragraph 5.1.3 Output current Limitation.
Optionally local control can be enabled and an analog input can be used to command the velocity control function.

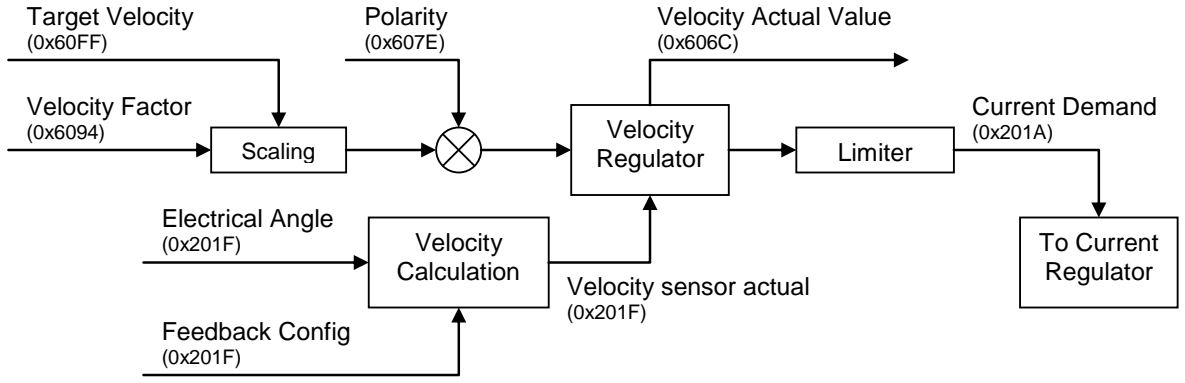
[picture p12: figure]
Scaling; Target Velocity (0x60FF); Velocity Factor (0x6094); Polarity (0x607E); Velocity; Regulator; Limiter; Current Demand (0x201A); Velocity Actual Value (0x606C); Velocity Calculation; Electrical Angle (0x201F); Feedback Config (0x201F); To Current Regulator Velocity sensor actual

Figure 0-5 Cyclic Sync Velocity – Block Diagram

5.1.2.7 Cyclic Sync Position

Cyclic Sync Position mode uses Target Position (0x607A) to command the position control function.
Find description for block “Limiter” in paragraph 5.1.3 Output current Limitation.
Optionally local control can be enabled and an analog input can be used to command the position control function.

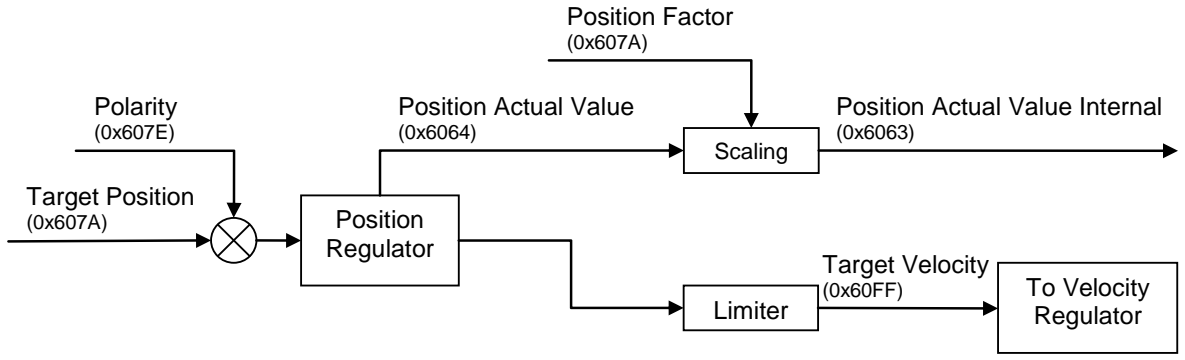
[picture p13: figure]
Target Position; Position; Regulator; Limiter; Position Actual Value (0x6064); Polarity (0x607E); Scaling; Position Actual Value Internal (0x6063); Position Factor (0x607A); Target Velocity; To Velocity

Figure 0-6 Cyclic Sync Position – Block Diagram

5.1.3 Output current Limitation
Output current limitation function is limiting Current Demand (0x201a) according limit values which can be set in objects:
- Motor Maximum Temperature (0x2058),
- Motor Maximum Temperature Gain (0x2059),
- Maximum Velocity (0x2052, 1),
- Maximum Velocity Gain (0x2052, 2),
- Undervoltage Limit (0x2055, 1),
- Undervoltage Limit Gain (0x2055, 2),
- Overvoltage Limit (0x2054),
- Stall Protection Current (0x205c),
- Stall Protection Time (0x205b).
Controller temperature is also monitored and it’s linearly for each degree of over temperature (85°C) limiting maximum current for 20% of maximum controller current.
If any of current limits are active, Warning Yellow LED will be turned on, also bit will be set in Warning (0x2027) according active limits.

Object description:

Entry description:
Access | Read
PDO mapping | Allowed
Default value | 0

Data description:

Index | 0x2027
Name | Warning
Data type | UNSIGNED16
Saved in EEPROM | No
Bit patern (MSB…LSB) | Description
0000 0000 0000 0001 | Controller Temperature
0000 0000 0000 0010 | Motor Temperature
0000 0000 0000 0100 | DC Link Under Voltage
0000 0000 0000 1000 | DC Link Over Voltage
0000 0000 0001 0000 | Stall
0000 0000 0010 0000 | Maximum Velocity

### 6 FEEDBACK CONFIG

0x2040: Feedback Config

In object Feedback Config (0x2040) user is able to set all settings according position feedback:
- Feedback Type
- Position Observer Enable
- Motor Phase Offset
- Feedback Direction
- Test Stepper Frequency
- Speed Filtering
- Motor Phase Offset Compensation
- Test Stepper Enable
- Auto Align Rotor Position Current

All feedback setting must be done in NMT state Preoperational. Parameters must be saved and the emDrive must be restarted.

6.1 0x2040, 1 Feedback Type

emDrive is supporting several different feedback types which are selectable through object Feedback Type (0x2040, 1).
Selection must be done in NMT state Preoperational.

Object description:
Index | 0x2040
Name | Feedback Type
Data type | UNSIGNED8
Saved in EEPROM | Yes

Entry description:

Data description:
Register data | Feedback type
0 | Constant Angle
1 | Hall Six Step Commutation
2 | SSI
3 | Resolver
4 | Sin / Cos
5 | Encoder
6 | Hall Predictive
7 … 255 | Reserved

Hint:
If using Motor with hall feedback (selected feedback Type Hall six step commutation or Hall predictive) Feedback resolution must be set to 6.
Access | Read / Write
PDO mapping | Allowed
Default value | 3

### 7 INPUTS AND OUTPUTS

### 7.1 Analog Inputs

The drive supports three analog inputs with resolution of 12bit (5V). One is used for motor temperature measurements, other two may be used for general purpose process values like reference for desired speed, torque or position etc.

Figure 7 Analog Inputs Block Diagram

7.1.1 Output data description
The output values are given in the object Analog Values. For each analog input voltage on AD pin can be read in corresponding Analog value.

### 7.2 Digital Inputs

The drive supports 3-6 digital inputs (depends of emDrive type). They may be used for general purpose process like enable FW, RW, Brake etc.

7.2.1 Output data description
The output values are given in the object Digital Values. Corresponding flag is set in object. Polarity of digital input is here already incorporated.

emDrive 400:
Din num. | Reserved | Din6 | Din5 | Din4 | Din3 | Din2 | Din1
Bit | 15 | 14 | 13 | 12 | 11 | 10 | 9 | 8 | 7 | 6 | 5 | 4 | 3 | 2 | 1 | 0

emDrive150, emDrive H300:
Din num. | Reserved | Din3 | Din2 | Din1
Bit | 15 | 14 | 13 | 12 | 11 | 10 | 9 | 8 | 7 | 6 | 5 | 4 | 3 | 2 | 1 | 0

Example:
If Din3 is active bit 13 will be set to 1 and value in register will be 0x0002.

Multiplier

Analog Input | Analog Value [CO object]
[Internal units 12bit] | [mV]

### 8 OBJECT DICTIONARY

8.1 0x1000 Device Type

Name | Device Type
Index | 0x1000
Subindex | 0x00
Type | UNSIGNED32
Access | RO
Stored in EEPROM | Yes
Default Value | 0x0192
Value range | 0 | 4294967295
Map to PDO | No

Description
This constant describes the device type. The value 0x0192 (400) mean that device follows the CiA Draft Standard Proposal 402, Device Profile Driver and Motion Control.

8.2 0x1001 Error register

Name | Error register
Index | 0x1001
Subindex | 0x00
Type | UNSIGNED8
Access | RO
Stored in EEPROM | No
Default Value | 0x00
Value range | 0 | 255
Map to PDO | Yes

Description
This object is an error register for the device. The device maps internal errors in this byte.

Related Objects

Table 2 Error register bits Bit Description

### 0 Generic Error 1 Current 2 Voltage 3 Temperature 4 Communication Error 5 Device Profile Defined Error 6 Reserved (always zero) 7 Manufacturer specific

8.3 0x1005 COB ID SYNC

Name | COB ID SYNC
Index | 0x1005
Subindex | 0x00
Type | UNSIGNED32
Access | RW
Stored in EEPROM | No
Default Value | 0x80
Value range | 0 | 4294967295
Map to PDO | No

Description
Communication Object Identifier of synchronization object.

8.4 0x1008 Manufacturer Device Name

Name | Manufacturer Device Name
Index | 0x1008
Subindex | 0x00
Type | VISIBLE_STRING
Access | RO
Stored in EEPROM | Yes
Default Value | EMSISO
Value range | 0 | 0
Map to PDO | No

Description
The product name is “EMSISO”

8.5 0x100b Node-ID

Name | Node-ID
Index | 0x100b
Subindex | 0x00
Type | UNSIGNED8
Access | RW
Stored in EEPROM | Yes
Default Value | 0x01
Value range | 1 | 255
Map to PDO | No

8.6 0x1010 Store Parameter Field

Name | Store Parameter Field
Index | 0x1010
Number of entries | 0x04
Name | Save all Parameters
Index | 0x1010
Subindex | 0x01
Type | VISIBLE_STRING
Access | RW
Stored in EEPROM | No
Default Value | 0
Value range | - | -
Map to PDO | No

Description
All parameters of device where stored in non volatile memory, if the code “save” is written to this object.
Byte | MSB | | | LSB
Character | ‘e’ | ‘v’ | ‘a’ | ‘s’
Hexvalue | 0x65 | 0x76 | 0x61 | 0x73

Controller must be restarted after this action is performed.

8.7 0x1011 Restore Default Parameters

Name | Restore Default Parameters
Index | 0x1011
Number of entries | 0x04
Name | Restore Default Parameters
Index | 0x1011
Subindex | 0x01
Type | VISIBLE_STRING
Access | RW
Stored in EEPROM | No
Default Value | 0
Value range | - | -
Map to PDO | No

Description
All parameters of device where restored with default values, if code “load” is written to this object.
Byte | MSB | | | LSB
Character | ‘d’ | ‘a’ | ‘o’ | ‘l’
Hexvalue | 0x64 | 0x61 | 0x6F | 0x6C

Controller must be restarted after this action is performed.

8.8 0x1014 COB ID EMCY

Name | COB ID EMCY
Index | 0x1014
Subindex | 0x00
Type | UNSIGNED32
Access | RW
Stored in EEPROM | No
Default Value | 0x80 + node ID
Value range | - | -
Map to PDO | No

Description
Communication Object Identifier of emergency object.

8.9 0x1017 Producer Heartbeat Time

Name | Producer Heartbeat Time
Index | 0x1017
Subindex | 0x00
Type | UNSIGNED16
Access | RW
Stored in EEPROM | Yes
Default Value | 0
Value range | 0 | 65535
Map to PDO | No

Description
This producer heartbeat time defines the cycle time of heartbeat. The producer heartbeat time is 0 if not used. The time has to be a multiple of 1ms.

Remarks
It’s not allowed for one device to use both error control mechanisms Guarding Protocol and Heartbeat Protocol at the same time. If the heartbeat producer time is equal to 0 the heartbeat protocol is used and the guarding protocol is disabled.

8.10 0x1018 Identity Object

Name | Identity Object
Index | 0x1018
Number of entries | 0x04
Name | Vendor Id
Index | 0x1018
Subindex | 0x01
Type | UNSIGNED32
Access | RO
Stored in EEPROM | -

Default Value | 000003C6
Value range | 0 | 4294967295
Map to PDO | No

Description
The CANopen vendor identification of “Emsiso emDrives”
Name | Product Code
Index | 0x1018
Subindex | 0x02
Type | UNSIGNED32
Access | RO
Stored in EEPROM | -
Default Value | -
Value range | - | -
Map to PDO | No
Name | Revision number
Index | 0x1018
Subindex | 0x03
Type | UNSIGNED32
Access | RO
Stored in EEPROM | -
Default Value | -
Value range | 0 | 4294967295
Map to PDO | No

Description

CAN revision | Drive Major revision | Drive Minor revision
xx | xx | xx

8.11 0x1021 Store EDS

Name | Store EDS
Index | 0x1021
Subindex | 0x00
Type | DOMAIN
Access | RW
Stored in EEPROM | -
Default Value | Not defined
Value range | - | -
Map to PDO | No

Description
The Store EDS includes Electronic Datasheet which is used for the node.

Remarks

The electronic datasheet is read and written according to the format specified in entry 0x1022.

8.12 0x1022 Storage Format

Name | Store EDS
Index | 0x1022
Subindex | 0x00
Type | UNSIGNED16
Access | RW
Stored in EEPROM | -
Default Value | Not defined
Value range | - | -
Map to PDO | No

Description
From FW version newer than 1.1.7 this entry defines the format that electronic datasheet is read from and written to entry 0x1021

Value Description
0x0000 Uncompressed ASCII
0x0001 .zip

0x1029 Error behavior

Name | Error behavior
Index | 0x1029
Number of entries | 0x01
Name | Communication Error
Index | 0x1029
Subindex | 0x01
Type | UNSIGNED8
Access | RW
Stored in EEPROM | Yes
Default Value | 0
Value range | 0 | 1
Map to PDO | No

Description
Value Description
0x0000 Switches to Pre-operational 0x0001 Does not change states

8.13 0x1200 Server SDO parameter

Name | Server SDO parameter
Index | 0x1200

Number of entries | 0x02
Name | COB ID Client to Server (Receive SDO)
Index | 0x1200
Subindex | 0x01
Type | UNSIGNED32
Access | RO
Stored in EEPROM | -
Default Value | Node ID + 0x600
Value range | - | -
Map to PDO | No

Description
The communication Object Identifier of service data objects from master to device is shown here.
Name | COB ID Server to Client (Transmit SDO)
Index | 0x1200
Subindex | 0x02
Type | UNSIGNED32
Access | RO
Stored in EEPROM | -
Default Value | Node ID + 0x580
Value range | - | -
Map to PDO | No

Description
The communication Object Identifier of service data objects from device to master is shown here.

8.14 0x1400 Receive PDO 1 Parameter

Name | Receive PDO 1 Parameter
Index | 0x1400
Number of entries | 0x05
Name | COB ID receive PDO 1
Index | 0x1400
Subindex | 0x01
Type | UNSIGNED32
Access | RW
Stored in EEPROM | -
Default Value | Node ID + 0x200
Value range | 0 | 4294967295
Map to PDO | No

Description
Communication Object Identifier of receive process data object 1.

Name | Transmission type receive PDO 1
Index | 0x1400
Subindex | 0x02
Type | UNSIGNED8
Access | RW
Stored in EEPROM | -
Default Value | 0xFE
Value range | 0 | 255
Map to PDO | No

Description
The transmission type describes how PDO communication works. The following types are supported:
Value Description

### 1 synchron

255 asynchron

8.15 0x1401 Receive PDO 2 parameter

Name | Receive PDO 2 Parameter
Index | 0x1401
Number of entries | 0x02
Name | COB ID receive PDO 2
Index | 0x1401
Subindex | 0x01
Type | UNSIGNED32
Access | RW
Stored in EEPROM | -
Default Value | Node Id + 0x300
Value range | 0 | 4294967295
Map to PDO | No

Description
Communication Object Identifier of receive process data object 2.
Name | Transmission type receive PDO 2
Index | 0x1401
Subindex | 0x02
Type | UNSIGNED8
Access | RW
Stored in EEPROM | -
Default Value | 0xFE
Value range | 0 | 255
Map to PDO | No

Description
The transmission type describes how PDO communication works. The following types are supported:
Value Description

### 1 synchron

255 asynchron

8.16 0x1402 Receive PDO 3 parameter

Name | Receive PDO 3 Parameter
Index | 0x1402
Number of entries | 0x02
Name | COB ID receive PDO 3
Index | 0x1402
Subindex | 0x01
Type | UNSIGNED32
Access | RW
Stored in EEPROM | -
Default Value | Node Id + 0x300
Value range | 0 | 4294967295
Map to PDO | No

Description
Communication Object Identifier of receive process data object 3.
Name | Transmission type receive PDO 3
Index | 0x1402
Subindex | 0x02
Type | UNSIGNED8
Access | RW
Stored in EEPROM | -
Default Value | 0xFE
Value range | 0 | 255
Map to PDO | No

Description
The transmission type describes how PDO communication works. The following types are supported:
Value Description

### 1 synchron

255 asynchron

8.17 0x1403 Receive PDO 4 parameter

Name | Receive PDO 4 Parameter
Index | 0x1403
Number of entries | 0x02
Name | COB ID receive PDO 4
Index | 0x1403
Subindex | 0x01
Type | UNSIGNED32

Access | RW
Stored in EEPROM | -
Default Value | Node Id + 0x300
Value range | 0 | 4294967295
Map to PDO | No

Description
Communication Object Identifier of receive process data object 2.
Name | Transmission type receive PDO 4
Index | 0x1403
Subindex | 0x02
Type | UNSIGNED8
Access | RW
Stored in EEPROM | -
Default Value | 0xFE
Value range | 0 | 255
Map to PDO | No

Description
The transmission type describes how PDO communication works. The following types are supported:
Value Description

### 1 Synchron

255 Asynchrony

8.18 0x1600 Receive PDO 1 Mapping

Name | Receive PDO 1 Parameter
Index | 0x1600
Number of entries | 0x08
Name | Number of mapped Aplication Objects in receive PDO
Index | 0x1600
Subindex | 0x00
Type | UNSIGNED8
Access | RW
Stored in EEPROM | -
Default Value | 3
Value range | 0 | 255
Map to PDO | No

Description
Changes in mapping are only possible in NMT state pre-operational. Before it’s possible to enable PDO, it’s necessary to map objects.
Value Description

### 0 PDO is disabled

1-8 | One to eight objects are mapped

34

/108

Name

1

st mapped object
Index | 0x1600
Subindex | 0x01
Type | UNSIGNED32
Access | RW
Stored in EEPROM | -
Default Value | 0x60400010
Value range | -
Map to PDO | No
Name | 2 nd mapped object
Index | 0x1600
Subindex | 0x02
Type | UNSIGNED32
Access | RW
Stored in EEPROM | -
Default Value | 0
Value range | -
Map to PDO | No
Name | 3 rd mapped object
Index | 0x1600
Subindex | 0x03
Type | UNSIGNED32
Access | RW
Stored in EEPROM | -
Default Value | 0
Value range | -
Map to PDO | No
Name | 4 th mapped object
Index | 0x1600
Subindex | 0x04
Type | UNSIGNED32
Access | RW
Stored in EEPROM | -
Default Value | 0
Value range | -
Map to PDO | No
Name | 5 th mapped object
Index | 0x1600
Subindex | 0x05
Type | UNSIGNED32
Access | RW
Stored in EEPROM | -
Default Value | 0
Value range | -
Map to PDO | No
Name | 7 th mapped object

Index | 0x1600
Subindex | 0x07
Type | UNSIGNED32
Access | RW
Stored in EEPROM | -
Default Value | 0
Value range | - | -
Map to PDO | No
Name | 8

th mapped object
Index | 0x1600
Subindex | 0x08
Type | UNSIGNED32
Access | RW
Stored in EEPROM | -
Default Value | 0
Value range | - | -
Map to PDO | No

Description
The objects that are supported to map are marked in each object Id description at the bottom area of table description: Map to PDO.

Remarks
Changes in mapping are only possible in NMT state pre-operational. To change a mapped object it is necessary to disable PDO. The maximal length of a process data object is 64 bit; because of this it is only possible to map two 32-bit values or two 16-bit values and one 32-bit value and so on.

8.19 0x1601 Receive PDO 2 mapping

Name | Receive PDO 2 Parameter
Index | 0x1601
Number of entries | 0x08
Name | Number of mapped Aplication Objects in receive PDO
Index | 0x1601
Subindex | 0x00
Type | UNSIGNED8
Access | RW
Stored in EEPROM | -
Default Value | 1
Value range | 0 | 255
Map to PDO | No

Description
Changes in mapping are only possible in NMT state pre-operational. Before it’s possible to enable PDO, it’s necessary to map objects.
Value Description

### 0 PDO is disabled

1-8 | One to eight objects are mapped
Name | 1

st mapped object
Index | 0x1601
Subindex | 0x01
Type | UNSIGNED32
Access | RW
Stored in EEPROM | -
Default Value | 0x60400010
Value range | - | -
Map to PDO | No
Name | 2

nd mapped object
Index | 0x1601
Subindex | 0x02
Type | UNSIGNED32
Access | RW
Stored in EEPROM | -
Default Value | 0
Value range | - | -
Map to PDO | No
Name | 3

rd mapped object
Index | 0x1601
Subindex | 0x03
Type | UNSIGNED32
Access | RW
Stored in EEPROM | -
Default Value | 0
Value range | - | -
Map to PDO | No
Name | 4

th mapped object
Index | 0x1601
Subindex | 0x04
Type | UNSIGNED32
Access | RW
Stored in EEPROM | -
Default Value | 0
Value range | - | -
Map to PDO | No
Name | 5

th mapped object
Index | 0x1601
Subindex | 0x05
Type | UNSIGNED32
Access | RW
Stored in EEPROM | -
Default Value | 0
Value range | - | -

Map to PDO | No
Name | 7

th mapped object
Index | 0x1601
Subindex | 0x07
Type | UNSIGNED32
Access | RW
Stored in EEPROM | -
Default Value | 0
Value range | - | -
Map to PDO | No
Name | 8

th mapped object
Index | 0x1601
Subindex | 0x08
Type | UNSIGNED32
Access | RW
Stored in EEPROM | -
Default Value | 0
Value range | - | -
Map to PDO | No

Description
The objects that are supported to map are marked in each object Id description at the bottom area of table description: Map to PDO.

Remarks
Changes in mapping are only possible in NMT state pre-operational. To change a mapped object it is necessary to disable PDO. The maximal length of a process data object is 64 bit; because of this it is only possible to map two 32-bit values or two 16-bit values and one 32-bit value and so on.

8.20 0x1602 Receive PDO 3 Mapping

Name | Receive PDO 3 Parameter
Index | 0x1602
Number of entries | 0x08
Name | Number of mapped Aplication Objects in receive PDO
Index | 0x1602
Subindex | 0x00
Type | UNSIGNED8
Access | RW
Stored in EEPROM | -
Default Value | 3
Value range | 0 | 255
Map to PDO | No

Description
Changes in mapping are only possible in NMT state pre-operational. Before it’s possible to enable PDO, it’s necessary to map objects.

Value Description

### 0 PDO is disabled

1-8 | One to eight objects are mapped
Name | 1

st mapped object
Index | 0x1602
Subindex | 0x01
Type | UNSIGNED32
Access | RW
Stored in EEPROM | -
Default Value | 0x60400010
Value range | - | -
Map to PDO | No
Name | 2

nd mapped object
Index | 0x1602
Subindex | 0x02
Type | UNSIGNED32
Access | RW
Stored in EEPROM | -
Default Value | 0
Value range | - | -
Map to PDO | No
Name | 3

rd mapped object
Index | 0x1602
Subindex | 0x03
Type | UNSIGNED32
Access | RW
Stored in EEPROM | -
Default Value | 0
Value range | - | -
Map to PDO | No
Name | 4

th mapped object
Index | 0x1602
Subindex | 0x04
Type | UNSIGNED32
Access | RW
Stored in EEPROM | -
Default Value | 0
Value range | - | -
Map to PDO | No
Name | 5

th mapped object
Index | 0x1602
Subindex | 0x05
Type | UNSIGNED32
Access | RW

Stored in EEPROM | -
Default Value | 0
Value range | - | -
Map to PDO | No
Name | 7

th mapped object
Index | 0x1602
Subindex | 0x07
Type | UNSIGNED32
Access | RW
Stored in EEPROM | -
Default Value | 0
Value range | - | -
Map to PDO | No
Name | 8

th mapped object
Index | 0x1602
Subindex | 0x08
Type | UNSIGNED32
Access | RW
Stored in EEPROM | -
Default Value | 0
Value range | - | -
Map to PDO | No

Description
The objects that are supported to map are marked in each object Id description at the bottom area of table description: Map to PDO.

Remarks
Changes in mapping are only possible in NMT state pre-operational. To change a mapped object it is necessary to disable PDO. The maximal length of a process data object is 64 bit; because of this it is only possible to map two 32-bit values or two 16-bit values and one 32-bit value and so on.

8.21 0x1603 Receive PDO 4 Mapping

Name | Receive PDO 4 Parameter
Index | 0x1603
Number of entries | 0x08
Name | Number of mapped Aplication Objects in receive PDO
Index | 0x1603
Subindex | 0x00
Type | UNSIGNED8
Access | RW
Stored in EEPROM | -
Default Value | 3
Value range | 0 | 255
Map to PDO | No

Description
Changes in mapping are only possible in NMT state pre-operational. Before it’s possible to enable PDO, it’s necessary to map objects.
Value Description

### 0 PDO is disabled

1-8 | One to eight objects are mapped
Name | 1

st mapped object
Index | 0x1603
Subindex | 0x01
Type | UNSIGNED32
Access | RW
Stored in EEPROM | -
Default Value | 0x60400010
Value range | - | -
Map to PDO | No
Name | 2

nd mapped object
Index | 0x1600
Subindex | 0x02
Type | UNSIGNED32
Access | RW
Stored in EEPROM | -
Default Value | 0
Value range | - | -
Map to PDO | No
Name | 3

rd mapped object
Index | 0x1603
Subindex | 0x03
Type | UNSIGNED32
Access | RW
Stored in EEPROM | -
Default Value | 0
Value range | - | -
Map to PDO | No
Name | 4

th mapped object
Index | 0x1603
Subindex | 0x04
Type | UNSIGNED32
Access | RW
Stored in EEPROM | -
Default Value | 0
Value range | - | -
Map to PDO | No
Name | 5

th mapped object
Index | 0x1603
Subindex | 0x05
Type | UNSIGNED32

Access | RW
Stored in EEPROM | -
Default Value | 0
Value range | - | -
Map to PDO | No
Name | 7

th mapped object
Index | 0x1603
Subindex | 0x07
Type | UNSIGNED32
Access | RW
Stored in EEPROM | -
Default Value | 0
Value range | - | -
Map to PDO | No
Name | 8

th mapped object
Index | 0x1603
Subindex | 0x08
Type | UNSIGNED32
Access | RW
Stored in EEPROM | -
Default Value | 0
Value range | - | -
Map to PDO | No

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

8.22 0x1800 Transimt PDO 1 parameter

Name | Transmit PDO 1 Parameter
Index | 0x1800
Number of entries | 0x06
Name | COB ID
Index | 0x1800
Subindex | 0x01
Type | UNSIGNED32
Access | RW
Stored in EEPROM | -
Default Value | Node ID + 0x180
Value range | - | -

Map to PDO | No

Description
Communication Object Identifier of transmit process data object 1.
Name | Transmission type transmit PDO 1
Index | 0x1800
Subindex | 0x02
Type | UNSIGNED8
Access | RW
Stored in EEPROM | -
Default Value | 0xFE
Value range | 0 | 255
Map to PDO | No

Description
The transmission type describes how PDO communication works. The following types are supported:
Value Description

### 1 Synchron

253 Asynchron on RTR only
255 Asynchron on change
Remarks
The transmission type 253 means that the PDO is only transmitted on remote transmission request (RTR). If transmission type 255 is selected the PDO is transmitted if the data’s change its values. The inhibit time defines a minimum interval therefore.
Name | Inhibit time transmit PDO 1
Index | 0x1800
Subindex | 0x03
Type | UNSIGNED16
Access | RW
Stored in EEPROM | -
Default Value | 65535
Value range | - | -
Map to PDO | No

Description
The time is the minimum interval for event triggered PDO transmison. The value is defined as multiple of 100µs.

Remarks
Event triggered PDOs can generate a huge CAN bus load also devise load especially if the inhibit time of different PDOs are set to a small value.

8.23 0x1801 Transmit PDO 2 parameter

Name | Transmit PDO 2 parameter
Index | 0x1801
Number of entries | 0x03

Name | COB ID transmit PDO 2
Index | 0x1801
Subindex | 0x01
Type | UNSIGNED32
Access | RW
Stored in EEPROM | -
Default Value | Node ID + 0x0280
Value range | 0x00000181 | 0x0000057F
Map to PDO | No

Description
Communication Object Identifier of transmit data object 2.
Name | Transmission type transmit PDO 2
Index | 0x1801
Subindex | 0x02
Type | UNSIGNED8
Access | RW
Stored in EEPROM | -
Default Value | 253
Value range | - | -
Map to PDO | No

Description
The transmission type describes how PDO communication works. The following types are supported:
Value Description

### 1 Synchron

253 Asynchron on RTR only
255 Asynchron on change

Remarks
The transmission type 253 means that the PDO is only transmitted on remote transmission request (RTR). If transmission type 255 is selected the PDO is transmitted if the data’s change its values. The inhibit time defines a minimum interval therefore.
Name | Inhibit time transmit PDO 2
Index | 0x1801
Subindex | 0x02
Type | UNSIGNED8
Access | RW
Stored in EEPROM | -
Default Value | 253
Value range | - | -
Map to PDO | No

Description
The transmission type describes how PDO communication works. The following types are supported:
Value Description

### 1 Synchron

253 Asynchron on RTR only
255 Asynchron on change

Remarks
The transmission type 253 means that the PDO is only transmitted on remote transmission request (RTR). If transmission type 255 is selected the PDO is transmitted if the data’s change its values. The inhibit time defines a minimum interval therefore.

8.24 0x1802 Transmit PDO 3 parameter

Name | Transmit PDO 3 parameter
Index | 0x1802
Number of entries | 0x03
Name | COB ID transmit PDO 3
Index | 0x1802
Subindex | 0x01
Type | UNSIGNED32
Access | RW
Stored in EEPROM | -
Default Value | Node ID + 0x0380
Value range | 0x00000181 | 0x0000057F
Map to PDO | No

Description
Communication Object Identifier of transmit process data object 3.
Name | Transmission type transmit PDO 3
Index | 0x1802
Subindex | 0x02
Type | UNSIGNED8
Access | RW
Stored in EEPROM | -
Default Value | 253
Value range | - | -
Map to PDO | No

Descritpion
The transmission type describes how PDO communication works. The following types are supported:
Value Description

### 1 Synchron

253 Asynchron on RTR only
255 Asynchron on change

Remarks
The transmission type 253 means that the PDO is only transmitted on remote transmission request (RTR). If transmission type 255 is selected the PDO is transmitted if the data’s change its values. The inhibit time defines a minimum interval therefore.
Name | Inhibit time transmit PDO 3

Index | 0x1802
Subindex | 0x03
Type | UNSIGNED16
Access | RW
Stored in EEPROM | -
Default Value | 65535
Value range | - | -
Map to PDO | No

Description
This time is the minimum interval for event triggered PDO transmission. The value is defined as multiple of 100μs.

Remarks
Event triggered PDOs can generate a huge CAN bus load and also device load especially if the inhibit time of different PDOs are set to a small value.

8.25 0x1803 Transmit PDO 4 parameter

Name | Transmit PDO 4 parameter
Index | 0x1803
Number of entries | 0x03
Name | COB ID transmit PDO 4
Index | 0x1803
Subindex | 0x01
Type | UNSIGNED32
Access | RW
Stored in EEPROM | -
Default Value | Node ID + 0x0480
Value range | 0x00000181 | 0x0000057F
Map to PDO | No

Description
Communication Object Identifier of transmit process data object 3.
Name | Transmission type transmit PDO 3
Index | 0x1803
Subindex | 0x02
Type | UNSIGNED8
Access | RW
Stored in EEPROM | -
Default Value | 253
Value range | - | -
Map to PDO | No

Descritpion
The transmission type describes how PDO communication works. The following types are supported:
Value Description

### 1 Synchron

253 Asynchron on RTR only
255 Asynchron on change

Remarks
The transmission type 253 means that the PDO is only transmitted on remote transmission request (RTR). If transmission type 255 is selected the PDO is transmitted if the data’s change its values. The inhibit time defines a minimum interval therefore.
Name | Inhibit time transmit PDO 4
Index | 0x1803
Subindex | 0x03
Type | UNSIGNED16
Access | RW
Stored in EEPROM | -
Default Value | 65535
Value range | - | -
Map to PDO | No

Description
This time is the minimum interval for event triggered PDO transmission. The value is defined as multiple of 100μs.

Remarks
Event triggered PDOs can generate a huge CAN bus load and also device load especially if the inhibit time of different PDOs are set to a small value.

8.26 0x1A00 Transmit PDO 1 mapping

Name | Transmit PDO 1 mapping
Index | 0x1A00
Number of entries | -
Name | Number of mapped Application Objects in transmit PDO
Index | 0x1A00
Subindex | 0x00
Type | UNSIGNED8
Access | RW
Stored in EEPROM | -
Default Value | 1
Value range | 0 | 8
Map to PDO | No

Remarks
Changes in mapping are only possible in NMT state pre-operational. Before it is possible to enable PDO, it is necessary to map objects.
Value Description

### 0 PDO is disabled

1-8 | One to eight objects are mapped

47

/108

Name

1

st mapped object
Index | 0x1A00
Subindex | 0x01
Type | UNSIGNED32
Access | RW
Stored in EEPROM | -
Default Value | 0x60400010
Value range | -
Map to PDO | No
Name | 2 nd mapped object
Index | 0x1A00
Subindex | 0x02
Type | UNSIGNED32
Access | RW
Stored in EEPROM | -
Default Value | 0
Value range | -
Map to PDO | No
Name | 3 rd mapped object
Index | 0x1A00
Subindex | 0x03
Type | UNSIGNED32
Access | RW
Stored in EEPROM | -
Default Value | 0
Value range | -
Map to PDO | No
Name | 4 th mapped object
Index | 0x1A00
Subindex | 0x04
Type | UNSIGNED32
Access | RW
Stored in EEPROM | -
Default Value | 0
Value range | -
Map to PDO | No
Name | 5 th mapped object
Index | 0x1A00
Subindex | 0x05
Type | UNSIGNED32
Access | RW
Stored in EEPROM | -
Default Value | 0
Value range | -
Map to PDO | No
Name | 7 th mapped object

Index | 0x1A00
Subindex | 0x07
Type | UNSIGNED32
Access | RW
Stored in EEPROM | -
Default Value | 0
Value range | - | -
Map to PDO | No
Name | 8

th mapped object
Index | 0x1A00
Subindex | 0x08
Type | UNSIGNED32
Access | RW
Stored in EEPROM | -
Default Value | 0
Value range | - | -
Map to PDO | No

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

8.27 0x1A01Transmit PDO 2 mapping

Name | Transmit PDO 2 mapping
Index | 0x1A01
Number of entries | -
Name | Number of mapped Application Objects in transmit PDO
Index | 0x1A01
Subindex | 0x00
Type | UNSIGNED8
Access | RW
Stored in EEPROM | -
Default Value | 1
Value range | 0 | 8
Map to PDO | No

Remarks
Changes in mapping are only possible in NMT state pre-operational. Before it is possible to enable PDO, it is necessary to map objects.
Value Description

### 0 PDO is disabled

1-8 | One to eight objects are mapped

Name | 1

st mapped object
Index | 0x1A01
Subindex | 0x01
Type | UNSIGNED32
Access | RW
Stored in EEPROM | -
Default Value | 0x60400010
Value range | - | -
Map to PDO | No
Name | 2

nd mapped object
Index | 0x1A01
Subindex | 0x02
Type | UNSIGNED32
Access | RW
Stored in EEPROM | -
Default Value | 0
Value range | - | -
Map to PDO | No
Name | 3

rd mapped object
Index | 0x1A01
Subindex | 0x03
Type | UNSIGNED32
Access | RW
Stored in EEPROM | -
Default Value | 0
Value range | - | -
Map to PDO | No
Name | 4

th mapped object
Index | 0x1A01
Subindex | 0x04
Type | UNSIGNED32
Access | RW
Stored in EEPROM | -
Default Value | 0
Value range | - | -
Map to PDO | No
Name | 5

th mapped object
Index | 0x1A01
Subindex | 0x05
Type | UNSIGNED32
Access | RW
Stored in EEPROM | -
Default Value | 0
Value range | - | -
Map to PDO | No

Name | 7

th mapped object
Index | 0x1A01
Subindex | 0x07
Type | UNSIGNED32
Access | RW
Stored in EEPROM | -
Default Value | 0
Value range | - | -
Map to PDO | No
Name | 8

th mapped object
Index | 0x1A01
Subindex | 0x08
Type | UNSIGNED32
Access | RW
Stored in EEPROM | -
Default Value | 0
Value range | - | -
Map to PDO | No

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

8.28 0x1A02 Transmit PDO 3 mapping

Name | Transmit PDO 3 mapping
Index | 0x1A02
Number of entries | -
Name | Number of mapped Application Objects in transmit PDO
Index | 0x1A02
Subindex | 0x00
Type | UNSIGNED8
Access | RW
Stored in EEPROM | -
Default Value | 1
Value range | 0 | 8
Map to PDO | No

Remarks
Changes in mapping are only possible in NMT state pre-operational. Before it is possible to enable PDO, it is necessary to map objects.
Value Description

51

/108

0 | PDO is disabled 1-8 | One to eight objects are mapped

Name

1

st mapped object
Index | 0x1A02
Subindex | 0x01
Type | UNSIGNED32
Access | RW
Stored in EEPROM | -
Default Value | 0x60400010
Value range | -
Map to PDO | No
Name | 2 nd mapped object
Index | 0x1A02
Subindex | 0x02
Type | UNSIGNED32
Access | RW
Stored in EEPROM | -
Default Value | 0
Value range | -
Map to PDO | No
Name | 3 rd mapped object
Index | 0x1A02
Subindex | 0x03
Type | UNSIGNED32
Access | RW
Stored in EEPROM | -
Default Value | 0
Value range | -
Map to PDO | No
Name | 4 th mapped object
Index | 0x1A02
Subindex | 0x04
Type | UNSIGNED32
Access | RW
Stored in EEPROM | -
Default Value | 0
Value range | -
Map to PDO | No
Name | 5 th mapped object
Index | 0x1A02
Subindex | 0x05
Type | UNSIGNED32
Access | RW
Stored in EEPROM | -
Default Value | 0

Value range | - | -
Map to PDO | No
Name | 7

th mapped object
Index | 0x1A02
Subindex | 0x07
Type | UNSIGNED32
Access | RW
Stored in EEPROM | -
Default Value | 0
Value range | - | -
Map to PDO | No
Name | 8

th mapped object
Index | 0x1A02
Subindex | 0x08
Type | UNSIGNED32
Access | RW
Stored in EEPROM | -
Default Value | 0
Value range | - | -
Map to PDO | No

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

8.29 0x1A03 Transmit PDO 4 mapping

Name | Transmit PDO 3 mapping
Index | 0x1A03
Number of entries | -
Name | Number of mapped Application Objects in transmit PDO
Index | 0x1A03
Subindex | 0x00
Type | UNSIGNED8
Access | RW
Stored in EEPROM | -
Default Value | 1
Value range | 0 | 8
Map to PDO | No

Remarks

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

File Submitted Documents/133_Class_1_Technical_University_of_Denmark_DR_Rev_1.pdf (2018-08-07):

### Initial Design parameter

The team have aimed to build a competitive car to compete against both electrical and IC cars. Being the first year of competition, the aim is to build a solid foundation for further developments the coming years.

### Suspension

The suspension design aims to keep it simple enough to allow full knowledge and understanding of all the contributions to the car’s kinematics from the different components. With limited, finite element analysis possibilities, the design needed to be relatively simple so primarily manual calculations could be used. The first choice there was made was to use an SKF hub bearing unit, which would simplify the production and assembly of the upright. Along with the hub bearing unit, 13’’ wheels where chosen to ensure freedom with the suspension geometry design. The geometry of the suspension is designed with a wish for a relatively high roll centre, which allows the car to have limited roll rate although the suspension design does not have an anti-roll bar. This made it possible to design the spring and damper connection directly between the lower A-arm and chassis, which significantly reduces the number of components needed. Furthermore, the soft wheel rate and front inclined roll axis should provide forgiving handling characteristics which are ideal for an inexperienced driver. The double wishbone suspension was designed with load paths as the primary focus. In figure XX the front A-arms can be seen (the spring and damper are not in this rendering). At the chassis mounting, rod-ends mounted axially in the tubes are used and at the upright, spherical bearings in a housing, which the tubes are welded to, are used. For the upright, a finite element method analysis was carried out. The upright is milled from an aluminium alloy (AW 6082 T6), which ensures low weight and excellent machinability. The brake disc material is cast iron which was found to be the most feasible option. Satisfying suspension geometry and a simple design to ensure a quick production was achieved.
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

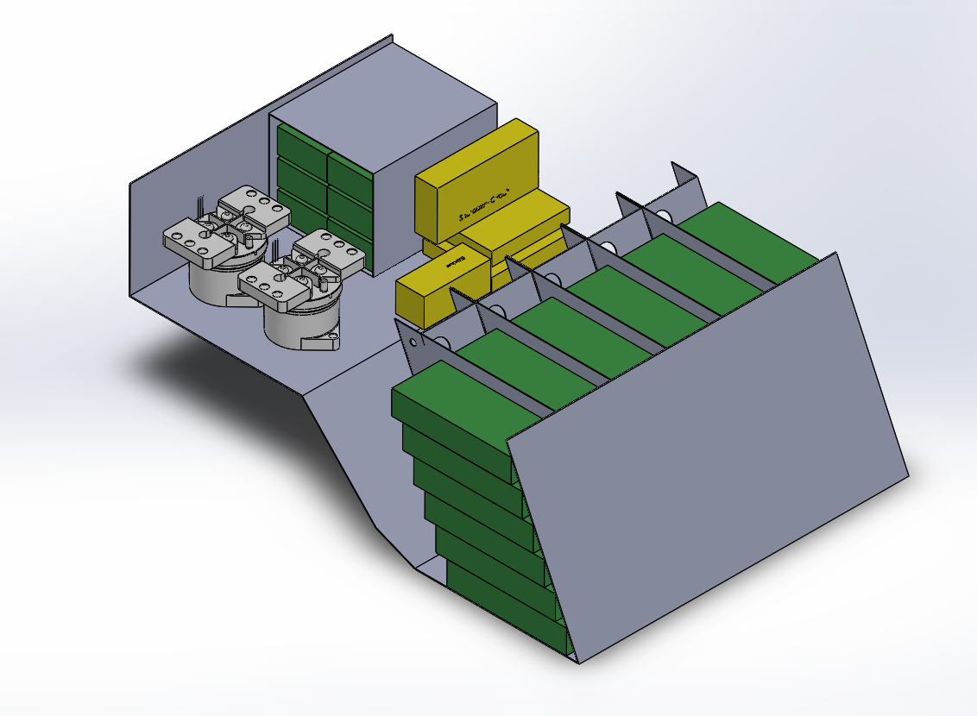
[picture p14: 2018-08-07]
Groups/Battery/Container Design/accumulator.PNG

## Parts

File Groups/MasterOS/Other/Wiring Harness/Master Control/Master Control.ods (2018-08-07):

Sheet: Master Control Overview
External reference | Bill of Materials for wiring harness |  |  |  |  | Part Listing |  |  | Cable Listing
MST | Item | Type | Part Number | Description | Quantity | Schematic Number | Part Number | Description | Cable Number | Part Number | Conductors
 | 1 | Cable | 54.83.594.031 | LIYCY-P twisted pair 0.5 mm2 cable |  | P1 | GLVS | Grounded Low Voltage System
 |  |  |  |  |  | C1 | NI 9853 | cRIO CAN interface
 |  |  |  |  |  | A1 |  | CAN interface for pedals and steering wheel
 |  |  |  |  |  | A2 |  | CAN interface for brake light and siren
 |  |  |  |  |  | A3 |  | CAN interface for cooling control
 |  |  |  |  |  | A4 |  | CAN interface for dashboard
 |  |  |  |  |  | B1 |  | Brake Light
 |  |  |  |  |  | B2 |  | Cooling System
 |  |  |  |  |  | B3 |  | Dashboard
 |  |  |  |  |  | B4 |  | Pedal sensor assembly
 |  |  |  |  |  | B5 |  | Steering wheel position sensor

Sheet: P1
Connector List |  | P1.V1 |  |  |  |  |  | P1.V2
Connector Number | Part Number | Cavity | To | Conductor | Colour | Gauge | Notes | Cavity | To | Conductor | Colour | Gauge | Notes
P1.V1 | ??? | 1 |  |  | Red |  | V+ | 1 |  |  | Red |  | V+
P1.V2 | ??? | 2 |  |  | Black |  | GND | 2 |  |  | Black |  | GND

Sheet: C1
Connector List |  | C1.CAN0 Connections
Connector Number | Part Number | Cavity | To | Conductor | Colour | Gauge | Notes
C1.CAN0 | DE9F | 1 | NC
C1.CAN1 | DE9F | 2 | MOT.S1.D.2 |  |  |  | CAN_L / SCS
 |  | 3 | MOT.S1.D.3 |  |  |  | COM / SCS
 |  | 4 | NC
 |  | 5 | MOT.S1.D.5 |  |  |  | SHLD
 |  | 6 | MOT.S1.D.6 |  |  |  | COM / SCS
 |  | 7 | MOT.S1.D.7 |  |  |  | CAN_H / SCS
 |  | 8 | NC
 |  | 9 | NC

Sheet: A1
Connector List |  | A1.C1 Connections |  |  |  |  |  | A1.C2 Connections |  |  |  |  |  | A1.C3 Connections |  |  |  |  |  | A1.C4 Connections |  |  |  |  |  | A1.C4 Connections
Connector Number | Part Number | Cavity | To | Conductor | Colour | Gauge | Notes | Cavity | To | Conductor | Colour | Gauge | Notes | Cavity | To | Conductor | Colour | Gauge | Notes | Cavity | To | Conductor | Colour | Gauge | Notes | Cavity | To | Conductor | Colour | Gauge | Notes
C1 | UTS7124PSCR | 1 |  |  | White | 0.5 mm2 | +12V | 1 |  |  | White | 0.5 mm2 | +5V | 1 |  |  | White | 0.5 mm2 | +5V | 1 |  |  | White | 0.5 mm2 | +5V | 1 | B5.C1.1 |  | White | 0.5 mm2 | +5V
C2 | UTS7124PSCR | 2 |  |  | Green | 0.5 mm2 | CAN H / SCS | 2 |  |  | Green | 0.5 mm2 | APPS1 / SCS | 2 |  |  | Green | 0.5 mm2 | BPPS1 | 2 |  |  | Green | 0.5 mm2 | BSPD1 / SCS | 2 | B5.C1.2 |  | Green | 0.5 mm2 | Steering Wheel Position
 |  | 3 |  |  | Yellow | 0.5 mm2 | CAN L / SCS | 3 |  |  | Yellow | 0.5 mm2 | APPS2 / SCS | 3 |  |  | Yellow | 0.5 mm2 | BPPS2 | 3 |  |  | Yellow | 0.5 mm2 | BSPD2 / SCS | 3 | NC |  | Yellow | 0.5 mm2
 |  | GND |  |  | Brown | 0.5 mm2 | GND | GND |  |  | Brown | 0.5 mm2 | GND | GND |  |  | Brown | 0.5 mm2 | GND | GND |  |  | Brown | 0.5 mm2 | GND | GND | B5.C1.GND |  | Brown | 0.5 mm2 | GND

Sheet: A2
Connector List |  | A2.C1 Connections |  |  |  |  |  | A2.C2 Connections
Connector Number | Part Number | Cavity | To | Conductor | Colour | Gauge | Notes | Cavity | To | Conductor | Colour | Gauge | Notes
C1 | UTS7124PSCR | 1 |  |  | White | 0.5 mm2 | +12V | 1 | B1.C1.1 |  | White | 0.5 mm2 | +12V
C2 | UTS7124PSCR | 2 |  |  | Green | 0.5 mm2 | CAN H | 2 | B1.C1.2 |  | Green | 0.5 mm2 | Brake Light Signal 1
 |  | 3 |  |  | Yellow | 0.5 mm2 | CAN L | 3 | B1.C1.3 |  | Yellow | 0.5 mm2 | Brake Light Signal 2
 |  | GND |  |  | Brown | 0.5 mm2 | GND | GND | B1.C1.GND |  | Brown | 0.5 mm2 | GND

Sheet: A3
Connector List |  | A3.C1 Connections |  |  |  |  |  | A3.C2 Connections
Connector Number | Part Number | Cavity | To | Conductor | Colour | Gauge | Notes | Cavity | To | Conductor | Colour | Gauge | Notes
C1 | UTS7124PSCR | 1 |  |  | White | 0.5 mm2 | +24V | 1 | B2.C1.1 |  | White | 0.5 mm2 | +24V
C2 | UTS7124PSCR | 2 |  |  | Green | 0.5 mm2 | CAN H | 2 | B2.C1.2 |  | Green | 0.5 mm2 | Cooling Pump Signal 1
 |  | 3 |  |  | Yellow | 0.5 mm2 | CAN L | 3 | B2.C1.3 |  | Yellow | 0.5 mm2 | Cooling Pump Signal 2
 |  | GND |  |  | Brown | 0.5 mm2 | GND | GND | B2.C1.GND |  | Brown | 0.5 mm2 | GND

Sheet: A4
Connector List |  | A4.C1 Connections
Connector Number | Part Number | Cavity | To | Conductor | Colour | Gauge | Notes
C1 | UTS7124PSCR | 1 |  |  | White | 0.5 mm2 | +12V
 |  | 2 |  |  | Green | 0.5 mm2 | CAN H
 |  | 3 |  |  | Yellow | 0.5 mm2 | CAN L
 |  | GND |  |  | Brown | 0.5 mm2 | GND

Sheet: B1
Connector List |  | B1.C1 Connections
Connector Number | Part Number | Cavity | To | Conductor | Colour | Gauge | Notes
C1 | UTS7124PSCR | 1 | A2.C2.1 |  | White |  | +12V
 |  | 2 | A2.C2.2 |  | Green |  | Brake Light Signal 1
 |  | 3 | A2.C2.3 |  | Yellow |  | Brake Light Signal 2
 |  | GND | A2.C2.GND |  | Brown |  | GND

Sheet: B2
Connector List |  | B2.C1 Connections
Connector Number | Part Number | Cavity | To | Conductor | Colour | Gauge | Notes
C1 | UTS7124PSCR | 1 | A3.C2.1 |  | White |  | +24V
 |  | 2 | A3.C2.2 |  | Green |  | Cooling Pump Signal 1
 |  | 3 | A3.C2.3 |  | Yellow |  | Cooling Pump Signal 2
 |  | GND | A3.C2.GND |  | Brown |  | GND

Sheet: B5
Connector List |  | B5.C1 Connections
Connector Number | Part Number | Cavity | To | Conductor | Colour | Gauge | Notes
C1 | UTS7124PSCR | 1 | A1.C4.1 |  | White |  | +5V
 |  | 2 | A1.C4.2 |  | Green |  | Steering Wheel Position
 |  | 3 | NC |  | Yellow
 |  | GND | A1.C4.GND |  | Brown |  | GND

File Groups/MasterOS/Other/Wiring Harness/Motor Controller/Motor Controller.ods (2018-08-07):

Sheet: Motor Controller Overview
External reference |  | Bill of Materials for wiring harness |  |  |  |  | Part Listing |  |  | Cable Listing
MOT |  | Item | Type | Part Number | Description | Quantity | Schematic Number | Part Number | Description | Cable Number | Part Number | Conductors | Length
 |  | 1 | Connector | TE Connectivity 776164-1 | Motor Controller Main Connector | 2 | MC1 | EmDrive 500 | Left Motor Controller | 1
 |  | 2 | Connector | RS241-4631 | M8 Crimp Terminal | 16 | MC2 | EmDrive 500 | Right Motor Controller | 2
 |  | 3 | Connector | DE9F | cRIO CAN Connector | 1 | M1 | EMRAX 228 | Left Motor | 3
 |  | 4 | Connector | RM44AC | Motor encoder wires | 2 | M2 | EMRAX 228 | Right Motor | 4
 |  | 5 | Connector | DE9M | CAN splitter connector | 1 | S1 | CAN_splitter | CAN splitter | 5
 |  | 6 | Cable | 54.83.594.031 | LIYCY-P twisted pair 2x2x0.5 mm2 cable |  | P1 | GLVS | Grounded Low Voltage System | 6
 |  | 7 | Cable | 54.83.594.073 | LIYCY-P twisted pair 4x2x0.5 mm2 cable |  | B1 | Accumulator Container | Battery power | 7
 |  |  |  |  |  |  | R1 | RS232_adapter | RS232 Adapter 1 | 8
 |  |  |  |  |  |  | R2 | RS232_adapter | RS232 Adapter 2 | 9
 |  |  |  |  |  |  | S2 | Ground_splitter | Ground splitter for temperature/hall 1 | 10
MANGLER: | shielding på CAN, størrelse og farve på ledninger, samling af kabler |  |  |  |  |  | S3 | Ground_splitter | Ground splitter for temperature/hall 2 | 11

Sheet: MC1
Connector List |  | MC1.U Connections |  |  |  |  |  | MC1.V Connections |  |  |  |  |  | MC1.W Connections |  |  |  |  |  | MC1.B+ Connections |  |  |  |  |  | MC1.B- Connections |  |  |  |  |  | MC1.A Connections
Connector Number | Part Number | Cavity | To | Conductor | Colour | Gauge | Notes | Cavity | To | Conductor | Colour | Gauge | Notes | Cavity | To | Conductor | Colour | Gauge | Notes | Cavity | To | Conductor | Colour | Gauge | Notes | Cavity | To | Conductor | Colour | Gauge | Notes | Cavity | To | Conductor | Colour | Gauge | Notes
MC1.U | RS241-4631 | 1 | M1.U |  | Orange | 50 mm2 | TS | 1 | M1.V |  | Orange | 50 mm2 | TS | 1 | M1.W |  | Orange | 50 mm2 | TS | 1 | B1.B+1 |  | Orange | 50 mm2 | TS | 1 | B1.B-1 |  | Orange | 50 mm2 | TS | 1 | P1.V1.2 |  | Black |  | GND Ignition / Power Supply -
MC1.V | RS241-4631 |  |  |  |  |  |  |  |  |  |  |  |  |  |  |  |  |  |  |  |  |  |  |  |  |  |  |  |  |  |  | 2 | P1.V1.1 |  | Red |  | Ignition / Power Supply +
MC1.W | RS241-4631 |  |  |  |  |  |  |  |  |  |  |  |  |  |  |  |  |  |  |  |  |  |  |  |  |  |  |  |  |  |  | 3 | R1.W.3 |  |  |  | Logic GND / RS232 GND
MC1.B+ | RS241-4631 |  |  |  |  |  |  |  |  |  |  |  |  |  |  |  |  |  |  |  |  |  |  |  |  |  |  |  |  |  |  | 4 | NC |  |  |  | Throttle Vcc Out
MC1.B- | RS241-4631 |  |  |  |  |  |  |  |  |  |  |  |  |  |  |  |  |  |  |  |  |  |  |  |  |  |  |  |  |  |  | 5 | NC |  |  |  | Throttle Input
MC1.A | TE Connectivity 776164-1 |  |  |  |  |  |  |  |  |  |  |  |  |  |  |  |  |  |  |  |  |  |  |  |  |  |  |  |  |  |  | 6 | NC |  |  |  | FW upgrade
 |  |  |  |  |  |  |  |  |  |  |  |  |  |  |  |  |  |  |  |  |  |  |  |  |  |  |  |  |  |  |  | 7 | R1.W.2 |  |  |  | RS232 TX
 |  |  |  |  |  |  |  |  |  |  |  |  |  |  |  |  |  |  |  |  |  |  |  |  |  |  |  |  |  |  |  | 8 | R1.W.1 |  |  |  | RS232 RX
 |  |  |  |  |  |  |  |  |  |  |  |  |  |  |  |  |  |  |  |  |  |  |  |  |  |  |  |  |  |  |  | 9 | NC |  |  |  | SSI Clock +
 |  |  |  |  |  |  |  |  |  |  |  |  |  |  |  |  |  |  |  |  |  |  |  |  |  |  |  |  |  |  |  | 10 | NC |  |  |  | SSI Clock -
 |  |  |  |  |  |  |  |  |  |  |  |  |  |  |  |  |  |  |  |  |  |  |  |  |  |  |  |  |  |  |  | 11 | NC |  |  |  | SSI Data +
 |  |  |  |  |  |  |  |  |  |  |  |  |  |  |  |  |  |  |  |  |  |  |  |  |  |  |  |  |  |  |  | 12 | NC |  |  |  | SSI Data -
 |  |  |  |  |  |  |  |  |  |  |  |  |  |  |  |  |  |  |  |  |  |  |  |  |  |  |  |  |  |  |  | 13 | NC |  |  |  | Forward digital input
 |  |  |  |  |  |  |  |  |  |  |  |  |  |  |  |  |  |  |  |  |  |  |  |  |  |  |  |  |  |  |  | 14 | NC |  |  |  | Reverse digital input
 |  |  |  |  |  |  |  |  |  |  |  |  |  |  |  |  |  |  |  |  |  |  |  |  |  |  |  |  |  |  |  | 15 | NC |  |  |  | Brake in switch
 |  |  |  |  |  |  |  |  |  |  |  |  |  |  |  |  |  |  |  |  |  |  |  |  |  |  |  |  |  |  |  | 16 | NC |  |  |  | Open collector output 1
 |  |  |  |  |  |  |  |  |  |  |  |  |  |  |  |  |  |  |  |  |  |  |  |  |  |  |  |  |  |  |  | 17 | NC |  |  |  | Open collector output 2
 |  |  |  |  |  |  |  |  |  |  |  |  |  |  |  |  |  |  |  |  |  |  |  |  |  |  |  |  |  |  |  | 18 | NC |  |  |  | Aux input 1
 |  |  |  |  |  |  |  |  |  |  |  |  |  |  |  |  |  |  |  |  |  |  |  |  |  |  |  |  |  |  |  | 19 | S1.W.2 |  |  |  | CAN GND
 |  |  |  |  |  |  |  |  |  |  |  |  |  |  |  |  |  |  |  |  |  |  |  |  |  |  |  |  |  |  |  | 20 | NC |  |  |  | Resolver exc +
 |  |  |  |  |  |  |  |  |  |  |  |  |  |  |  |  |  |  |  |  |  |  |  |  |  |  |  |  |  |  |  | 21 | NC |  |  |  | Resolver exc -
 |  |  |  |  |  |  |  |  |  |  |  |  |  |  |  |  |  |  |  |  |  |  |  |  |  |  |  |  |  |  |  | 22 | M1.E.3 |  |  | 0.5 mm2 | Sin/cos sin
 |  |  |  |  |  |  |  |  |  |  |  |  |  |  |  |  |  |  |  |  |  |  |  |  |  |  |  |  |  |  |  | 23 | M1.E.4 |  |  | 0.5 mm2 | Sin/cos cos
 |  |  |  |  |  |  |  |  |  |  |  |  |  |  |  |  |  |  |  |  |  |  |  |  |  |  |  |  |  |  |  | 24 | S2.W2.1 |  |  |  | Hall GND
 |  |  |  |  |  |  |  |  |  |  |  |  |  |  |  |  |  |  |  |  |  |  |  |  |  |  |  |  |  |  |  | 25 | NC |  |  |  | Hall phase 1
 |  |  |  |  |  |  |  |  |  |  |  |  |  |  |  |  |  |  |  |  |  |  |  |  |  |  |  |  |  |  |  | 26 | NC |  |  |  | Hall phase 2
 |  |  |  |  |  |  |  |  |  |  |  |  |  |  |  |  |  |  |  |  |  |  |  |  |  |  |  |  |  |  |  | 27 | NC |  |  |  | Hall phase 3
 |  |  |  |  |  |  |  |  |  |  |  |  |  |  |  |  |  |  |  |  |  |  |  |  |  |  |  |  |  |  |  | 28 | M1.E.1 |  |  | 0.5 mm2 | Hall Vcc
 |  |  |  |  |  |  |  |  |  |  |  |  |  |  |  |  |  |  |  |  |  |  |  |  |  |  |  |  |  |  |  | 29 | M1.T.1 |  |  | 0.5 mm2 | Motor temperature
 |  |  |  |  |  |  |  |  |  |  |  |  |  |  |  |  |  |  |  |  |  |  |  |  |  |  |  |  |  |  |  | 30 | S1.W.1 |  |  |  | CANL
 |  |  |  |  |  |  |  |  |  |  |  |  |  |  |  |  |  |  |  |  |  |  |  |  |  |  |  |  |  |  |  | 31 | S1.W.4 |  |  |  | CANH
 |  |  |  |  |  |  |  |  |  |  |  |  |  |  |  |  |  |  |  |  |  |  |  |  |  |  |  |  |  |  |  | 32 | NC |  |  |  | Resolver sine +
 |  |  |  |  |  |  |  |  |  |  |  |  |  |  |  |  |  |  |  |  |  |  |  |  |  |  |  |  |  |  |  | 33 | NC |  |  |  | Resolver sine -
 |  |  |  |  |  |  |  |  |  |  |  |  |  |  |  |  |  |  |  |  |  |  |  |  |  |  |  |  |  |  |  | 34 | NC |  |  |  | Resolver cos +
 |  |  |  |  |  |  |  |  |  |  |  |  |  |  |  |  |  |  |  |  |  |  |  |  |  |  |  |  |  |  |  | 35 | NC |  |  |  | Resolver cos -

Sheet: MC2
Connector List |  | MC2.U Connections |  |  |  |  |  | MC2.V Connections |  |  |  |  |  | MC2.W Connections |  |  |  |  |  | MC2.B+ Connections |  |  |  |  |  | MC2.B- Connections |  |  |  |  |  | MC2.A Connections
Connector Number | Part Number | Cavity | To | Conductor | Colour | Gauge | Notes | Cavity | To | Conductor | Colour | Gauge | Notes | Cavity | To | Conductor | Colour | Gauge | Notes | Cavity | To | Conductor | Colour | Gauge | Notes | Cavity | To | Conductor | Colour | Gauge | Notes | Cavity | To | Conductor | Colour | Gauge | Notes
MC2.U | RS241-4631 | 1 | M2.U |  | Orange | 50 mm2 | TS | 1 | M2.V |  | Orange | 50 mm2 | TS | 1 | M2.W |  | Orange | 50 mm2 | TS | 1 | B1.B+2 |  | Orange | 50 mm2 | TS | 1 | B1.B-2 |  | Orange | 50 mm2 | TS | 1 | P1.V2.2 |  | Black |  | GND Ignition / Power Supply -
MC2.V | RS241-4631 |  |  |  |  |  |  |  |  |  |  |  |  |  |  |  |  |  |  |  |  |  |  |  |  |  |  |  |  |  |  | 2 | P1.V2.1 |  | Red |  | Ignition / Power Supply +
MC2.W | RS241-4631 |  |  |  |  |  |  |  |  |  |  |  |  |  |  |  |  |  |  |  |  |  |  |  |  |  |  |  |  |  |  | 3 | R2.W.3 |  | Black |  | Logic GND / RS232 GND
MC2.B+ | RS241-4631 |  |  |  |  |  |  |  |  |  |  |  |  |  |  |  |  |  |  |  |  |  |  |  |  |  |  |  |  |  |  | 4 | NC |  |  |  | Throttle Vcc Out
MC2.B- | RS241-4631 |  |  |  |  |  |  |  |  |  |  |  |  |  |  |  |  |  |  |  |  |  |  |  |  |  |  |  |  |  |  | 5 | NC |  |  |  | Throttle Input
MC2.A | TE Connectivity 776164-1 |  |  |  |  |  |  |  |  |  |  |  |  |  |  |  |  |  |  |  |  |  |  |  |  |  |  |  |  |  |  | 6 | NC |  |  |  | FW upgrade
 |  |  |  |  |  |  |  |  |  |  |  |  |  |  |  |  |  |  |  |  |  |  |  |  |  |  |  |  |  |  |  | 7 | R2.W.2 |  |  |  | RS232 TX
 |  |  |  |  |  |  |  |  |  |  |  |  |  |  |  |  |  |  |  |  |  |  |  |  |  |  |  |  |  |  |  | 8 | R2.W.1 |  |  |  | RS232 RX
 |  |  |  |  |  |  |  |  |  |  |  |  |  |  |  |  |  |  |  |  |  |  |  |  |  |  |  |  |  |  |  | 9 | NC |  |  |  | SSI Clock +
 |  |  |  |  |  |  |  |  |  |  |  |  |  |  |  |  |  |  |  |  |  |  |  |  |  |  |  |  |  |  |  | 10 | NC |  |  |  | SSI Clock -
 |  |  |  |  |  |  |  |  |  |  |  |  |  |  |  |  |  |  |  |  |  |  |  |  |  |  |  |  |  |  |  | 11 | NC |  |  |  | SSI Data +
 |  |  |  |  |  |  |  |  |  |  |  |  |  |  |  |  |  |  |  |  |  |  |  |  |  |  |  |  |  |  |  | 12 | NC |  |  |  | SSI Data -
 |  |  |  |  |  |  |  |  |  |  |  |  |  |  |  |  |  |  |  |  |  |  |  |  |  |  |  |  |  |  |  | 13 | NC |  |  |  | Forward digital input
 |  |  |  |  |  |  |  |  |  |  |  |  |  |  |  |  |  |  |  |  |  |  |  |  |  |  |  |  |  |  |  | 14 | NC |  |  |  | Reverse digital input
 |  |  |  |  |  |  |  |  |  |  |  |  |  |  |  |  |  |  |  |  |  |  |  |  |  |  |  |  |  |  |  | 15 | NC |  |  |  | Brake in switch
 |  |  |  |  |  |  |  |  |  |  |  |  |  |  |  |  |  |  |  |  |  |  |  |  |  |  |  |  |  |  |  | 16 | NC |  |  |  | Open collector output 1
 |  |  |  |  |  |  |  |  |  |  |  |  |  |  |  |  |  |  |  |  |  |  |  |  |  |  |  |  |  |  |  | 17 | NC |  |  |  | Open collector output 2
 |  |  |  |  |  |  |  |  |  |  |  |  |  |  |  |  |  |  |  |  |  |  |  |  |  |  |  |  |  |  |  | 18 | NC |  |  |  | Aux input 1
 |  |  |  |  |  |  |  |  |  |  |  |  |  |  |  |  |  |  |  |  |  |  |  |  |  |  |  |  |  |  |  | 19 | S1.W.6 |  |  |  | CAN GND
 |  |  |  |  |  |  |  |  |  |  |  |  |  |  |  |  |  |  |  |  |  |  |  |  |  |  |  |  |  |  |  | 20 | NC |  |  |  | Resolver exc +
 |  |  |  |  |  |  |  |  |  |  |  |  |  |  |  |  |  |  |  |  |  |  |  |  |  |  |  |  |  |  |  | 21 | NC |  |  |  | Resolver exc -
 |  |  |  |  |  |  |  |  |  |  |  |  |  |  |  |  |  |  |  |  |  |  |  |  |  |  |  |  |  |  |  | 22 | M2.E.3 |  | Black | 5 mm | Sin/cos sin
 |  |  |  |  |  |  |  |  |  |  |  |  |  |  |  |  |  |  |  |  |  |  |  |  |  |  |  |  |  |  |  | 23 | M2.E.4 |  | Brown | 5 mm | Sin/cos cos
 |  |  |  |  |  |  |  |  |  |  |  |  |  |  |  |  |  |  |  |  |  |  |  |  |  |  |  |  |  |  |  | 24 | S3.W2.1 |  |  |  | Hall GND
 |  |  |  |  |  |  |  |  |  |  |  |  |  |  |  |  |  |  |  |  |  |  |  |  |  |  |  |  |  |  |  | 25 | NC |  |  |  | Hall phase 1
 |  |  |  |  |  |  |  |  |  |  |  |  |  |  |  |  |  |  |  |  |  |  |  |  |  |  |  |  |  |  |  | 26 | NC |  |  |  | Hall phase 2
 |  |  |  |  |  |  |  |  |  |  |  |  |  |  |  |  |  |  |  |  |  |  |  |  |  |  |  |  |  |  |  | 27 | NC |  |  |  | Hall phase 3
 |  |  |  |  |  |  |  |  |  |  |  |  |  |  |  |  |  |  |  |  |  |  |  |  |  |  |  |  |  |  |  | 28 | M2.E.1 |  | Red | 5 mm | Hall Vcc
 |  |  |  |  |  |  |  |  |  |  |  |  |  |  |  |  |  |  |  |  |  |  |  |  |  |  |  |  |  |  |  | 29 | M2.T.1 |  | Black |  | Motor temperature
 |  |  |  |  |  |  |  |  |  |  |  |  |  |  |  |  |  |  |  |  |  |  |  |  |  |  |  |  |  |  |  | 30 | S1.W.5 |  |  |  | CANL
 |  |  |  |  |  |  |  |  |  |  |  |  |  |  |  |  |  |  |  |  |  |  |  |  |  |  |  |  |  |  |  | 31 | S1.W.8 |  |  |  | CANH
 |  |  |  |  |  |  |  |  |  |  |  |  |  |  |  |  |  |  |  |  |  |  |  |  |  |  |  |  |  |  |  | 32 | NC |  |  |  | Resolver sine +
 |  |  |  |  |  |  |  |  |  |  |  |  |  |  |  |  |  |  |  |  |  |  |  |  |  |  |  |  |  |  |  | 33 | NC |  |  |  | Resolver sine -
 |  |  |  |  |  |  |  |  |  |  |  |  |  |  |  |  |  |  |  |  |  |  |  |  |  |  |  |  |  |  |  | 34 | NC |  |  |  | Resolver cos +
 |  |  |  |  |  |  |  |  |  |  |  |  |  |  |  |  |  |  |  |  |  |  |  |  |  |  |  |  |  |  |  | 35 | NC |  |  |  | Resolver cos -

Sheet: M1
Connector List |  | M1.U Connections |  |  |  |  |  | M1.V Connections |  |  |  |  |  | M1.W Connections |  |  |  |  |  | M1.E Connections |  |  |  |  |  | M1.T Connections
Connector Number | Part Number | Cavity | To | Conductor | Colour | Gauge | Notes | Cavity | To | Conductor | Colour | Gauge | Notes | Cavity | To | Conductor | Colour | Gauge | Notes | Cavity | To | Conductor | Colour | Gauge | Notes | Cavity | To | Conductor | Colour | Gauge | Notes
M1.U | RS241-4631 | 1 | MC1.U |  | Orange | 50 mm2 | TS | 1 | MC1.V |  | Orange | 50 mm2 | TS | 1 | MC1.W |  | Orange | 50 mm2 | TS | 1 | MC1.A.28 |  | Red | 5 mm | Vdd | 1 | MC1.A.29 |  | Black |  | It does not seem to matter which wire is connected to what
M1.V | RS241-4631 |  |  |  |  |  |  |  |  |  |  |  |  |  |  |  |  |  |  | 2 | S2.W1.1 |  | Orange | 5 mm | GND | 2 | S2.W1.2 |  | Black |  | It does not seem to matter which wire is connected to what
M1.W | RS241-4631 |  |  |  |  |  |  |  |  |  |  |  |  |  |  |  |  |  |  | 3 | MC1.A.22 |  | Black | 5 mm | VA
M1.E | RM44AC |  |  |  |  |  |  |  |  |  |  |  |  |  |  |  |  |  |  | 4 | MC1.A.23 |  | Brown | 5 mm | VB
M1.T | (bare wire) |  |  |  |  |  |  |  |  |  |  |  |  |  |  |  |  |  |  | Shield

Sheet: M2
Connector List |  | M2.U Connections |  |  |  |  |  | M2.V Connections |  |  |  |  |  | M2.W Connections |  |  |  |  |  | M2.E Connections |  |  |  |  |  | M2.T Connections
Connector Number | Part Number | Cavity | To | Conductor | Colour | Gauge | Notes | Cavity | To | Conductor | Colour | Gauge | Notes | Cavity | To | Conductor | Colour | Gauge | Notes | Cavity | To | Conductor | Colour | Gauge | Notes | Cavity | To | Conductor | Colour | Gauge | Notes
M2.U | RS241-4631 | 1 | MC2.U |  | Orange | 50 mm2 | TS | 1 | MC2.V |  | Orange | 50 mm2 | TS | 1 | MC2.W |  | Orange | 50 mm2 | TS | 1 | MC2.A.28 |  | Red | 5 mm | Vdd | 1 | MC2.A.29 |  | Black |  | It does not seem to matter which wire is connected to what
M2.V | RS241-4631 |  |  |  |  |  |  |  |  |  |  |  |  |  |  |  |  |  |  | 2 | S3.W1.1 |  | Orange | 5 mm | GND | 2 | S3.W1.2 |  | Black |  | It does not seem to matter which wire is connected to what
M2.W | RS241-4631 |  |  |  |  |  |  |  |  |  |  |  |  |  |  |  |  |  |  | 3 | MC2.A.22 |  | Black | 5 mm | VA
M2.E | RM44AC |  |  |  |  |  |  |  |  |  |  |  |  |  |  |  |  |  |  | 4 | MC2.A.23 |  | Brown | 5 mm | VB
M2.T | (bare wire) |  |  |  |  |  |  |  |  |  |  |  |  |  |  |  |  |  |  | Shield

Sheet: S1
Connector List |  | S1.D Connections |  |  |  |  |  | S1.W Connections
Connector Number | Part Number | Cavity | To | Conductor | Colour | Gauge | Notes | Cavity | To | Conductor | Colour | Gauge | Notes
S1.D | DE9M | 1 | NC |  |  |  |  | 1 | MC1.A.30 |  |  |  | CAN_L
S1.W | (bare wire) | 2 | MST.C1.CAN0.2 |  |  |  | CAN_L | 2 | MC1.A.19 |  |  |  | COM
 |  | 3 | MST.C1.CAN0.3 |  |  |  | COM | 3 |  |  |  |  | SHLD
 |  | 4 | NC |  |  |  |  | 4 | MC1.A.31 |  |  |  | CAN_H
 |  | 5 | MST.C1.CAN0.5 |  |  |  | SHLD | 5 | MC2.A.30 |  |  |  | CAN_L
 |  | 6 | MST.C1.CAN0.6 |  |  |  | COM | 6 | MC2.A.19 |  |  |  | COM
 |  | 7 | MST.C1.CAN0.7 |  |  |  | CAN_H | 7 |  |  |  |  | SHLD
 |  | 8 | NC |  |  |  |  | 8 | MC2.A.31 |  |  |  | CAN_H
 |  | 9 | NC

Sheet: P1
Connector List |  | P1.V1 |  |  |  |  |  | P1.V2
Connector Number | Part Number | Cavity | To | Conductor | Colour | Gauge | Notes | Cavity | To | Conductor | Colour | Gauge | Notes
P1.V1 | ??? | 1 | MC1.A.2 |  | Red |  | V+ | 1 | MC2.A.2 |  | Red |  | V+
P1.V2 | ??? | 2 | MC1.A.1 |  | Black |  | GND | 2 | MC2.A.1 |  | Black |  | GND

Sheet: B1
Connector List |  | B1.B+1 |  |  |  |  |  | B1.B-1 |  |  |  |  |  | B1.B+2 |  |  |  |  |  | B1.B-2
Connector Number | Part Number | Cavity | To | Conductor | Colour | Gauge | Notes | Cavity | To | Conductor | Colour | Gauge | Notes | Cavity | To | Conductor | Colour | Gauge | Notes | Cavity | To | Conductor | Colour | Gauge | Notes
B1.B+1 | RS241-4631 | 1 | MC1.B+ |  | Orange | 50 mm2 | TS | 1 | MC1.B- |  | Orange | 50 mm2 | TS | 1 | MC2.B+ |  | Orange | 50 mm2 | TS | 1 | MC2.B- |  | Orange | 50 mm2 | TS
B1.B-1 | RS241-4631
B1.B+2 | RS241-4631
B1.B-2 | RS241-4631

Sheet: R1
Connector List |  | R1.D Connections |  |  |  |  |  | R1.W Connections
Connector Number | Part Number | Cavity | To | Conductor | Colour | Gauge | Notes | Cavity | To | Conductor | Colour | Gauge | Notes
R1.D | DE9F | 1 | NC |  |  |  |  | 1 | MC1.A.8 |  |  |  | RXD
R1.W | (bare wire) | 2 | NC |  |  |  | Optionally connect to PC RXD | 2 | MC1.A.7 |  |  |  | TXD
 |  | 3 | NC |  |  |  | Optionally connect to PC TXD | 3 | MC1.A.3 |  | Black |  | GND
 |  | 4 | NC
 |  | 5 | NC
 |  | 6 | NC
 |  | 7 | NC
 |  | 8 | NC
 |  | 9 | NC |  |  |  | Optionally connect to PC GND

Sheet: R2
Connector List |  | R2.D Connections |  |  |  |  |  | R2.W Connections
Connector Number | Part Number | Cavity | To | Conductor | Colour | Gauge | Notes | Cavity | To | Conductor | Colour | Gauge | Notes
R2.D | DE9F | 1 | NC |  |  |  |  | 1 | MC2.A.8 |  |  |  | RXD
R2.W | (bare wire) | 2 | NC |  |  |  | Optionally connect to PC RXD | 2 | MC2.A.7 |  |  |  | TXD
 |  | 3 | NC |  |  |  | Optionally connect to PC TXD | 3 | MC2.A.3 |  | Black |  | GND
 |  | 4 | NC
 |  | 5 | NC
 |  | 6 | NC
 |  | 7 | NC
 |  | 8 | NC
 |  | 9 | NC |  |  |  | Optionally connect to PC GND

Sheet: S2
Connector List |  | S2.W1 Connections |  |  |  |  |  | S2.W2 Connections
Connector Number | Part Number | Cavity | To | Conductor | Colour | Gauge | Notes | Cavity | To | Conductor | Colour | Gauge | Notes
S2.W1 | (bare wire) | 1 | M1.E.2 |  | Orange | 5 mm | Hall GND | 1 | MC1.A.24
S2.W2 | (bare wire) | 2 | M1.T.2 |  | Black |  | Temperature GND

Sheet: S3
Connector List |  | S3.W1 Connections |  |  |  |  |  | S3.W2 Connections
Connector Number | Part Number | Cavity | To | Conductor | Colour | Gauge | Notes | Cavity | To | Conductor | Colour | Gauge | Notes
S3.W1 | (bare wire) | 1 | M2.E.2 |  | Orange | 5 mm | Hall GND | 1 | MC2.A.24
S3.W2 | (bare wire) | 2 | M2.T.2 |  | Black |  | Temperature GND

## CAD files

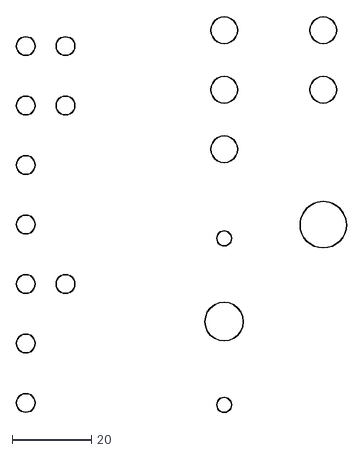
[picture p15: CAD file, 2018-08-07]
Groups/MasterOS/Other/testrig_cuttable.dxf
83.3 x 100.0

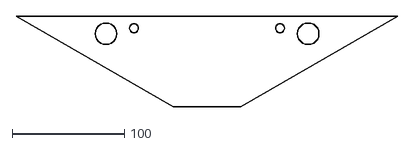
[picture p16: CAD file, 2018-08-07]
Groups/MasterOS/Other/dashboard2.dxf
339.6 x 80.7

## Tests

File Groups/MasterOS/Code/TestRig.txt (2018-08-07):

Ting der skal være på dashboard
	IMD failure light
	AMS failure light
	E-stop
	Tractive system activation button
	Ready to drive button
	(Info screen)

Ting der skal være på test-rig
	Steering wheel potentiometer
	Brake pedal potentiometers
	Accelerator pedal potentiometers
	Motor Current potentiometer
	Tractive System active button - EV5.11.6

	Cooling Pump Signal Indicators
	Brake Light Signal Indicators
	Ready To Drive Sound Indicator
	BSPD Activation Indicator
	Motor Control Signal Indicator
	APPS/Brake Pedal Plausibility Check Indicator - EV2.4
	Tractive System Active Indicator

Husk T10.4.4 - at mange ting skal tænde når man starter op

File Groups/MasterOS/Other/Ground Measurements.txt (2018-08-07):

Main grounding point: Tube 17
Resistance Tube 6: 0.08
Resistance Tube 1 (top): 0.05
Resistance Tube 21: 0.11
Resistance Tube 29: 0.08
Resistance Tube 34: 0.12
Resistance Undercarriage Back: 0.1
Resistance Lower Steering Column: 0.04
Resistance Steering Wheel Mount: 0.16

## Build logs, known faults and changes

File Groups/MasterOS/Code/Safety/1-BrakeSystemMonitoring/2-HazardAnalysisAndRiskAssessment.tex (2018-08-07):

\section{Hazard analysis and risk assessment}
% Reference: DS/ISO 26262-3 section 7.4.1.1 -- 7.4.4.2
%
% Pre-requisites:
%    - Item definition
%
% The item is evaluated based ONLY on the item definition, i.e. WITHOUT considering
% internal safety mechanisms that are already implemented or are planned.
% Safety mechanisms that are intended to be implemented are instead part of the
% functional safety concept.
% 
% Reference: DS/ISO 26262-3 section 7.4.1

\subsection{Pre-existing information}
% This section is for further supporting information such as
%    - Change impact analysis if applicable (only for existing items being changed)
%    - Relevant information on other independent items
%
% Reference: DS/ISO 26262-3 section 7.3.2
The brake system monitoring is a new item, so there will be no change impact.

\subsection{Situation analysis}
% The operational situations and operating modes in which an item's malfunctioning
% behaviour will result in a hazardous event are described.
% Consider both situations when the vehicle is correctly used AND when it is
% incorrectly used in a foreseeable manner.
% It is NOT necessary to consider situations in which the item is not expected to
% behave safely, i.e. when driving off-road.
%
% Required information:
%   - List of situations/modes in which the item may malfunction in a hazardous way
%
% Reference: DS/ISO 26262-3 section 7.4.2.1
The following situations will be considered:
\begin{description}
\item [1-OS1] Standstill - tractive system inactive
\item [1-OS2] Standstill - tractive system active
\item [1-OS3] Driving straight - constant speed
\item [1-OS4] Driving straight - accelerating
\item [1-OS5] Driving straight - decelerating
\item [1-OS6] Entering corner - constant speed
\item [1-OS7] Entering corner - accelerating
\item [1-OS8] Entering corner - decelerating
\item [1-OS9] Exiting corner - constant speed
\item [1-OS10] Exiting corner - accelerating
\item [1-OS11] Exiting corner - decelerating
\item [1-OS12] Being pushed
\item [1-OS13] Undergoing maintenance/repairs.
\end{description}

\subsection{Hazard identification}
% Identify hazards systematically using e.g. brainstorming, FMEA and tests.
%
% A hazard is a potential source of harm caused by malfunctioning behaviour.
% A hazard is defined in terms of conditions or behaviour that can be observed at
% the vehicle level assuming every other independent item/system is functioning
% correctly.
% A hazard can have many potential causes related to the implementation of the item,
% but these do NOT need to be considered in this hazard analysis and risk assessment,
% which is derived from a functional behaviour of the item.
The following hazards will be considered:
\begin{description}
\item [1-HZ1] Brake light shining when not braking
\item [1-HZ2] Brake light not shining when braking
\end{description}

% A hazardous event is a combination of a hazard and an operational situation.
% A hazardous event may have several simultaneous consequences, which must be
% considered together.
%
% Required information:
%    - List of hazards that can be observed at the vehicle level
%    - List of hazardous events for combinations of hazards and operational situations
%    - The consequences of each hazardous event
%
% Reference: DS/ISO 26262-3 section 7.4.2.2
% Definitions: DS/ISO 26262-1 term 1.57 -- 1.59
The operational situations and the hazards result in the following possible hazardous events:
\begin{center}
\begin{tabular}{l|l|l|l}
Operational situation	& Hazard	& Hazardous event	& Consequences \\
1-OS1			& 1-HZ1	& 1-OS1-HZ1			& No danger since vehicle is stationary with tractive system inactive. \\
1-OS1			& 1-HZ2	& 1-OS1-HZ2			& No danger even though bystanders may think driver is about to accelerate when he is not. \\
1-OS2			& 1-HZ1	& 1-OS2-HZ1			& Bystanders may believe vehicle is staying stationary, while driver may actually be about to accelerate. \\
1-OS2			& 1-HZ2	& 1-OS2-HZ2			& No danger even though bystanders may think driver is about to accelerate. \\
1-OS3			& 1-HZ1	& 1-OS3-HZ1			& Bystanders may believe vehicle is about to slow down, while it will actually maintain constant speed. \\
1-OS3			& 1-HZ2	& 1-OS3-HZ2			& If another vehicle is close behind while braking, the driver of the other vehicle may not be able to react in time. \\
1-OS4			& 1-HZ1	& 1-OS4-HZ1			& No danger, though the driver of another vehicle close behind may be confused by the situation. \\
1-OS4			& 1-HZ2	& 1-OS4-HZ2			& If another vehicle is close behind while braking, the driver of the other vehicle may not be able to react in time. \\
1-OS5			& 1-HZ1	& 1-OS5-HZ1			& Low danger, though if another vehicle is close behind while decelerating, the driver of the other vehicle may believe that the vehicle is decelerating faster than what is the case. \\
1-OS5			& 1-HZ2	& 1-OS5-HZ2			& If another vehicle is close behind while decelerating, the driver of the other vehicle may not be able to react in time. \\
1-OS6			& 1-HZ1	& 1-OS6-HZ1			& Low danger, though if another vehicle is close behind, the driver of the other vehicle may believe that the vehicle is decelerating. \\
1-OS6			& 1-HZ2	& 1-OS6-HZ2			& If another vehicle is close behind while braking, the driver of the other vehicle may not be able to react in time. \\
1-OS7			& 1-HZ1	& 1-OS7-HZ1			& No danger, though the driver of another vehicle close behind may be confused by the situation. \\
1-OS7			& 1-HZ2	& 1-OS7-HZ2			& If another vehicle is close behind while braking, the driver of the other vehicle may not be able to react in time. \\
1-OS8			& 1-HZ1	& 1-OS8-HZ1			& Low danger, though if another vehicle is close behind while decelerating, the driver of the other vehicle may believe that the vehicle is decelerating faster than what is the case. \\
1-OS8			& 1-HZ2	& 1-OS8-HZ2			& If another vehicle is close behind while decelerating, the driver of the other vehicle may not be able to react in time. \\
1-OS9			& 1-HZ1	& 1-OS9-HZ1			& Low danger, though if another vehicle is close behind, the driver of the other vehicle may believe that the vehicle is decelerating. \\
1-OS9			& 1-HZ2	& 1-OS9-HZ2			& If another vehicle is close behind while braking, the driver of the other vehicle may not be able to react in time. \\
1-OS10			& 1-HZ1	& 1-OS10-HZ1			& No danger, though the driver of another vehicle close behind may be confused by the situation. \\
1-OS10			& 1-HZ2	& 1-OS10-HZ2			& If another vehicle is close behind while braking, the driver of the other vehicle may not be able to react in time. \\
1-OS11			& 1-HZ1	& 1-OS11-HZ1			& No danger, though if another vehicle is close behind while decelerating, the driver of the other vehicle may believe that the vehicle is decelerating faster than what is the case. \\
1-OS11			& 1-HZ2	& 1-OS11-HZ2			& If another vehicle is close behind while decelerating, the driver of the other vehicle may not be able to react in time. \\
1-OS12			& 1-HZ1	& 1-OS12-HZ1			& No danger, though pushing crew may be surprised. \\
1-OS12			& 1-HZ2	& 1-OS12-HZ2			& No danger, though pushing crew may be surprised. \\
1-OS13			& 1-HZ1	& 1-OS13-HZ1			& No danger. \\
1-OS13			& 1-HZ2	& 1-OS13-HZ2			& No danger.
\end{tabular}
\end{center}

\subsection{Classification of hazardous events}
% All hazardous events shall be classified, unless they are outside the scope of
% DS/ISO 26262, e.g.  electric shock or fires not directly caused by malfunctioning
% E/E systems.
%
% If there is doubt about the classification of a hazard, it should be classified 
% conservatively, i.e. a higher ASIL classification shall be given rather than a lower.
%
% Required information for each hazardous event:
%    - Estimate of severity class of potential harm from the event
%    - Probability class of exposure of each operational situation causing the event
%    - Estimate of controllability class of the event
%    - An ASIL for the event using the above parameters, ensuring that the operational
%      situations are not too granular so the exposure classes are inappropriately low
%
% References:
%	DS/ISO 26262-3 section 7.4.3 -- 7.4.4.2
%    - Severity class: DS/ISO 26262-3 Table 1
%    - Exposure probability class: DS/ISO 26262-3 Table 2
%    - Controllability class: DS/ISO 26262-3 Table 3
%    - ASIL determination: DS/ISO 26262-3 Table 4
\begin{center}
\begin{tabular}{l|l|l|l|l}
Hazardous event	& Severity	& Exposure probability	& Controllability	& ASIL	\\
1-OS1-HZ1			& S0		& E1					& C0				& N/A	\\
1-OS1-HZ2			& S0		& E1					& C0				& N/A	\\
1-OS2-HZ1			& S3		& E3					& C0				& N/A	\\
1-OS2-HZ2			& S0		& E3					& C0				& N/A	\\
1-OS3-HZ1			& S3		& E2					& C0				& N/A	\\
1-OS3-HZ2			& S1		& E2					& C3				& QM	\\
1-OS4-HZ1			& S0		& E4					& C0				& N/A	\\
1-OS4-HZ2			& S3		& E4					& C3				& D		\\
1-OS5-HZ1			& S0		& E2					& C0				& N/A	\\
1-OS5-HZ2			& S2		& E2					& C3				& A		\\
1-OS6-HZ1			& S0		& E3					& C0				& N/A	\\
1-OS6-HZ2			& S1		& E3					& C2				& QM	\\
1-OS7-HZ1			& S1		& E3					& C0				& N/A	\\
1-OS7-HZ2			& S2		& E3					& C2				& A		\\
1-OS8-HZ1			& S1		& E4					& C0				& N/A	\\
1-OS8-HZ2			& S3		& E4					& C1				& B		\\
1-OS9-HZ1			& S0		& E3					& C0				& N/A	\\
1-OS9-HZ2			& S1		& E3					& C2				& QM	\\
1-OS10-HZ1			& S0		& E4					& C1				& N/A	\\
1-OS10-HZ2			& S1		& E4					& C3				& B		\\
1-OS11-HZ1			& S1		& E3					& C0				& N/A	\\
1-OS11-HZ2			& S1		& E3					& C1				& QM	\\
1-OS12-HZ1			& S0		& E3					& C0				& N/A	\\
1-OS12-HZ2			& S0		& E3					& C0				& N/A	\\
1-OS13-HZ1			& S0		& E4					& C0				& N/A	\\
1-OS13-HZ2			& S0		& E4					& C0				& N/A
\end{tabular}
\end{center}

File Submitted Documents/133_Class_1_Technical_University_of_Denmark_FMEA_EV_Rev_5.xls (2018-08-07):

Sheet: Intro
FS2018 - FMEA
Car Number | 133
University | Technical University of Denmark
This template contains two of examples of how to fill out the FMEA. Furthermore, it contains a number of failure modes which are both starting points and examples for the failures to be covered in your team's FMEA. NOTE: Not every given failure may apply to every team's system. The given failures may also be incomplete with respect to your specific system. Add failures to the list, if appropriate for your system.
Change the two complete examples given, i.e. No.1 and 2, to suit your system. Add missing failure modes with respect to your car's system. Be as complete as possible, adding any failures that affect the safety of your car, the driver, or other persons. Before submitting your FMEA please make sure it is complete. This way you will avoid unnecessary delays and queries. Please have a look at the document "How to pass ESF&FMEA" in the "Rules&Important Document, before filling out the FMEA form.
Edit the coloured cells to your specific data and reset the cell colour to white
Only add additional failures at the end of the list to keep the numbering scheme of the original template. This makes reviewing the document much easier and thus faster. Do not delete any failures, if they do not apply to your system. Just write "Does not apply." or similar with a short reason why.
Do not change the template's format!

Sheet: Definitions + Sev, Occ, Det
FMEA definitions of column headers and Key for Severity, Occurance and Detection ratings
Rating | Severity (Sev) | Occurrence (Occ) | Detection (Det)
1 | No injuries may be caused, but general safety is affected by this failure | Failure occurrence is very unlikely | Certain detection of the failure
2 | Light injuries may be caused by this failure | Relatively few failure occurrence | High chance of detecting this failure
3 | Medium injuries may be caused by this failure | Occasional failure occurrence | Medium chance of detecting this failure
4 | Heavy injuries may be caused by this failure | Frequent failure occurrence | Low chance of detecting this failure
5 | Fatal injuries may be caused by this failure | Persistent failure occurrence | Failure cannot be detected
Component/Item | The system or component that is affected
Function | What the system or component does
Failure Mode | The method by which the component fails
Failure Cause | The root cause of the failure
Failure Effect Local | What happens locally to the component as a consequence of the failure
Failure Effect Global | What happens to other systems or the rest of the vehicle as a consequence of the failure
Sev | The severity rating - see table above
Severity Reasoning | Your reasoning for the severity rating that is given
Occ | The likelihood of the occurrence - see table above
Occurrence Reasoning | Your reasoning for the occurance rating that is given
Failure Detection | How will the failure be detected - what are the systems on the car that detect this
Det | The rating for failure detection - see table
Detection Reasoning | Your reasoning for the failure detection rating
Risk | Calculated automatically from Sev, Occ and Det
Failure Handling - Vehicle | Once a failure has been detected, what is the immediate reaction of the ECU / BMS and the driver to mitigate the risk
Failure Handling - Team | How do you determine what has failed and what type of action is taken to remedy this? What precautions do you take whilst doing this?

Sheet: FMEA
FS 2018 FMEA
 | Car No.: | 133 | University: | Technical University of Denmark |  | Contact: | Robin Swann - racswann@gmail.com, Albert Seligmann - s163906@student.dtu.dk, Frederik Højlund - s163921@student.dtu.dk Jacob Vinther - s153561@student.dtu.dk
FMEA No.: | Component/Item | Function | Failure Mode | Failure Cause | Failure Effect |  | Sev | Severity Reasoning | Occ | Occurrence Reasoning | Failure Detection | Det | Detection Reasoning | Risk | Failure Handling - Vehicle | Failure Handling - Team | Comments | Feedback
 |  |  |  |  | Local | Global
1 | Tractive System Wiring | Energy transfer | Positive pole lost isolation to GLVS | Wiring insulation degradation | Potentially dangerous condition if operator touches the negative pole of the battery and the chassis | Possible chassis reference voltage potential change | 4 | Burns by electric arc, bruises and fractures caused by uncontrolled muscle movement due to the electric shock. Ventricular fibrillation not likely with DC voltages up to 600V, therefore not severity 5 | 2 | All wire insulations chosen with respect to the environment, additional thermal oder mechanical protection attached where needed, all wires are securely attached and professionaly built to lower the risk of damages by vibrations | Insulation resistance monitoring system. | 1 | IMD detects every isolation failure to the chassis, since the chassis is connected to control system ground | 8 | Isolation Lost Alarm enabled. IMD opens the AIRs through the Shutdown Circuit | Appropriate procedure to be executed once the car back in the PIT to restore the isolation. Fault to be identified and rectified before enabling the AIRs. Insulating gloves to be used | Applies to all following Failure Handling fields: Insulating gloves will be used whenever HV, TS og a shortcircuit is involved. In this case there will also always be atleast one other person supervising incase anything happens. | ok
2 | Tractive System Wiring | Energy transfer | Negative pole lost isolation to the GLVS | Wiring insulation degradation | Potentially dangerous condition if operator touches the positive pole of the battery and the chassis | Possible chassis reference voltage potential change | 4 | Burns by electric arc, bruises and fractures caused by uncontrolled muscle movement due to the electric shock. Ventricular fibrillation not likely with DC voltages up to 600V, therefore not severity 5 | 2 | All wire insulations chosen with respect to the environment, additional thermal oder mechanical protection attached where needed, all wires are securely attached and professionaly built to lower the risk of damages by vibrations | Insulation resistance monitoring system. | 1 | IMD detects every isolation failure to the chassis, since the chassis is connected to control system ground | 8 | Isolation Lost Alarm enabled. IMD opens the AIRs through the Shutdown Circuit | Appropriate procedure to be executed once the car back in the PIT to restore the isolation. Fault to be identified and rectified before enabling the AIRs. Insulating gloves to be used |  | ok
3 | Tractive System Wiring | Energy transfer | Open/live tractive system connections when switching on the tractive system | Improper circuit implementation. Mechanical damage. Lack of insulation | Dangerous if anyone comes in contact with live connections | Likely improper startup leading to shutdown | 4 | Serious damage could occur from electrocution | 2 | All circuitry will be double checked by several people, but can still occur due to mechanical damage | Detected by IMD/ECU | 2 | Should be detected by the IMD or ECU due to improper startup | 16 | Improper startup alarm will be enabled and shutdown will be engaged | Wiring will be checked and fixed using proper safety precautions |  | ok
4 | HVD / Tractive System Connectors | Energy transfer | HVD / Tractive System Connectors become lose while driving and eventually open up, exposing live contacts | Mechanical damage. Improper fastening of connectors | Dangerous if anyone comes in contact with live connections | Loss of TS power | 5 | The driver will loose control over tractive system. Risk of electricution. | 2 | Will be part of startup checklist | Detected by ECU | 2 | ECU will detect a shutdown with no shutdown notification signal recieved | 20 | Improper shutdown alarm will be enabled and shutdown will be engaged | The driver should stay in the car to prevent contact with conducting materials in the car while getting out. The ESO will secure and reconnect the HVD wearing insulated gloves. |  | ok
5 | Tractive System Fusing | Protection of tractive system wiring | Overcurrent is higher than the maximum switch off current of the used fuse | Faulty fuse. Short circuit. | Damage to circuitry through overcurrent | Wiring may get very hot and burn. Eventual loss of power. Improper discharging of battery, leading to battery damage | 5 | Serious damage could occur from electrocution. Most wiring will be destroyed. Most components will likely be destroyed. Fire likely | 1 | The switchoff current of the fuse greatly exceeds any possible overcurrent | Detected by BMS | 3 | AMS should be able to detect the overcurrent, but might overflow if the current is high enough. | 15 | The BMS will initiate shutdown | The driver should leave the car imidiately while preventing contact with conducting materials in the car while getting out. The ESO will disconnect the HVD wearing insulated gloves. |  | ok
6 | Accumulator | Energy Storage | Cell temperature above data sheet specification for discharging | cell overcurrent or cooling system malfunction. Poor connection causing high resistance | Surrounding cells get hot causing higher resistance and potentially even higher temperature if not dealt with. accumuleter can get hot. Solderjoints can come undone | chasis and surrounding components can get hot. Worst case: the accumulator can cause a fire | 4 | accumulator malfunction can potentially cause a fire or even an explosion if not dealt with properly. | 2 | The battery container will contain active cooling, the cells should never reach datasheet spec or 60 degrees even at high draw. | Detected by temperature sensor | 1 | The cells are monitored by many temperature sensors making it almost impossible for overheating to go undetected | 8 | Power will be cut from motors. Regenerative breaking will be disabled. Shutdown will be engaged | The driver should imidiately stop the vehicle and exit the vehicle. The team should standby with fire extinguishers. If the temperature is still rising action should be taken to mitigate the temperature rise, and if the temperature is dropping the team should wait untill it stabilizes. The temperature will be able to be monitored remotely. Once stable, the accumulator will be disconnected using the HVD and the accumulator will be inspected. |  | ok
7 | Accumulator | Energy Storage | Cell temperature above data sheet specification for charging | cell charge overcurrent or cooling system malfunction. Poor connection causing high resistance | cells in parallel get hot aswell causing higher resistance and potentially even higher temperature if not dealt with. accumuleter can get hot. Solderjoints can come undone | chasis and surrounding components can get hot. Worst case: the accumulator can cause a fire | 3 | accumulator malfunction can potentially cause a fire or even an explosion if not dealt with properly. Severity lower than charging because noone is in the car while charging | 1 | If the accumulator is charged with an appropriate charging current and voltage this should not occur. | Detected by temperature sensor | 1 | The cells are monitored by many temperature sensors making it almost impossible for overheating to go undetected | 3 | The charger is disconnected immediately. | The accumulator is inspected and the charging current is lowered for next time. |  | ok
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

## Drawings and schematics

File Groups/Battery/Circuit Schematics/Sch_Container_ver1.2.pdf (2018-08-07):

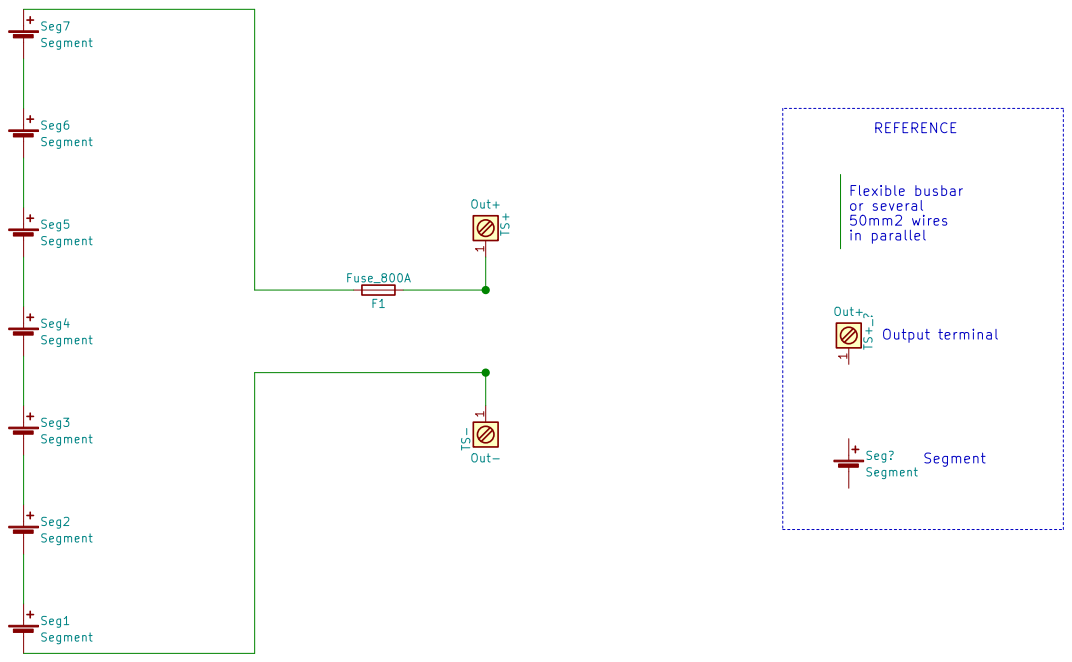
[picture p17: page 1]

1 TS- Out- Flexible busbar or several 50mm2 wires

Id: 1/1 Title: File: Container.sch Sheet: / Seg1
Segment

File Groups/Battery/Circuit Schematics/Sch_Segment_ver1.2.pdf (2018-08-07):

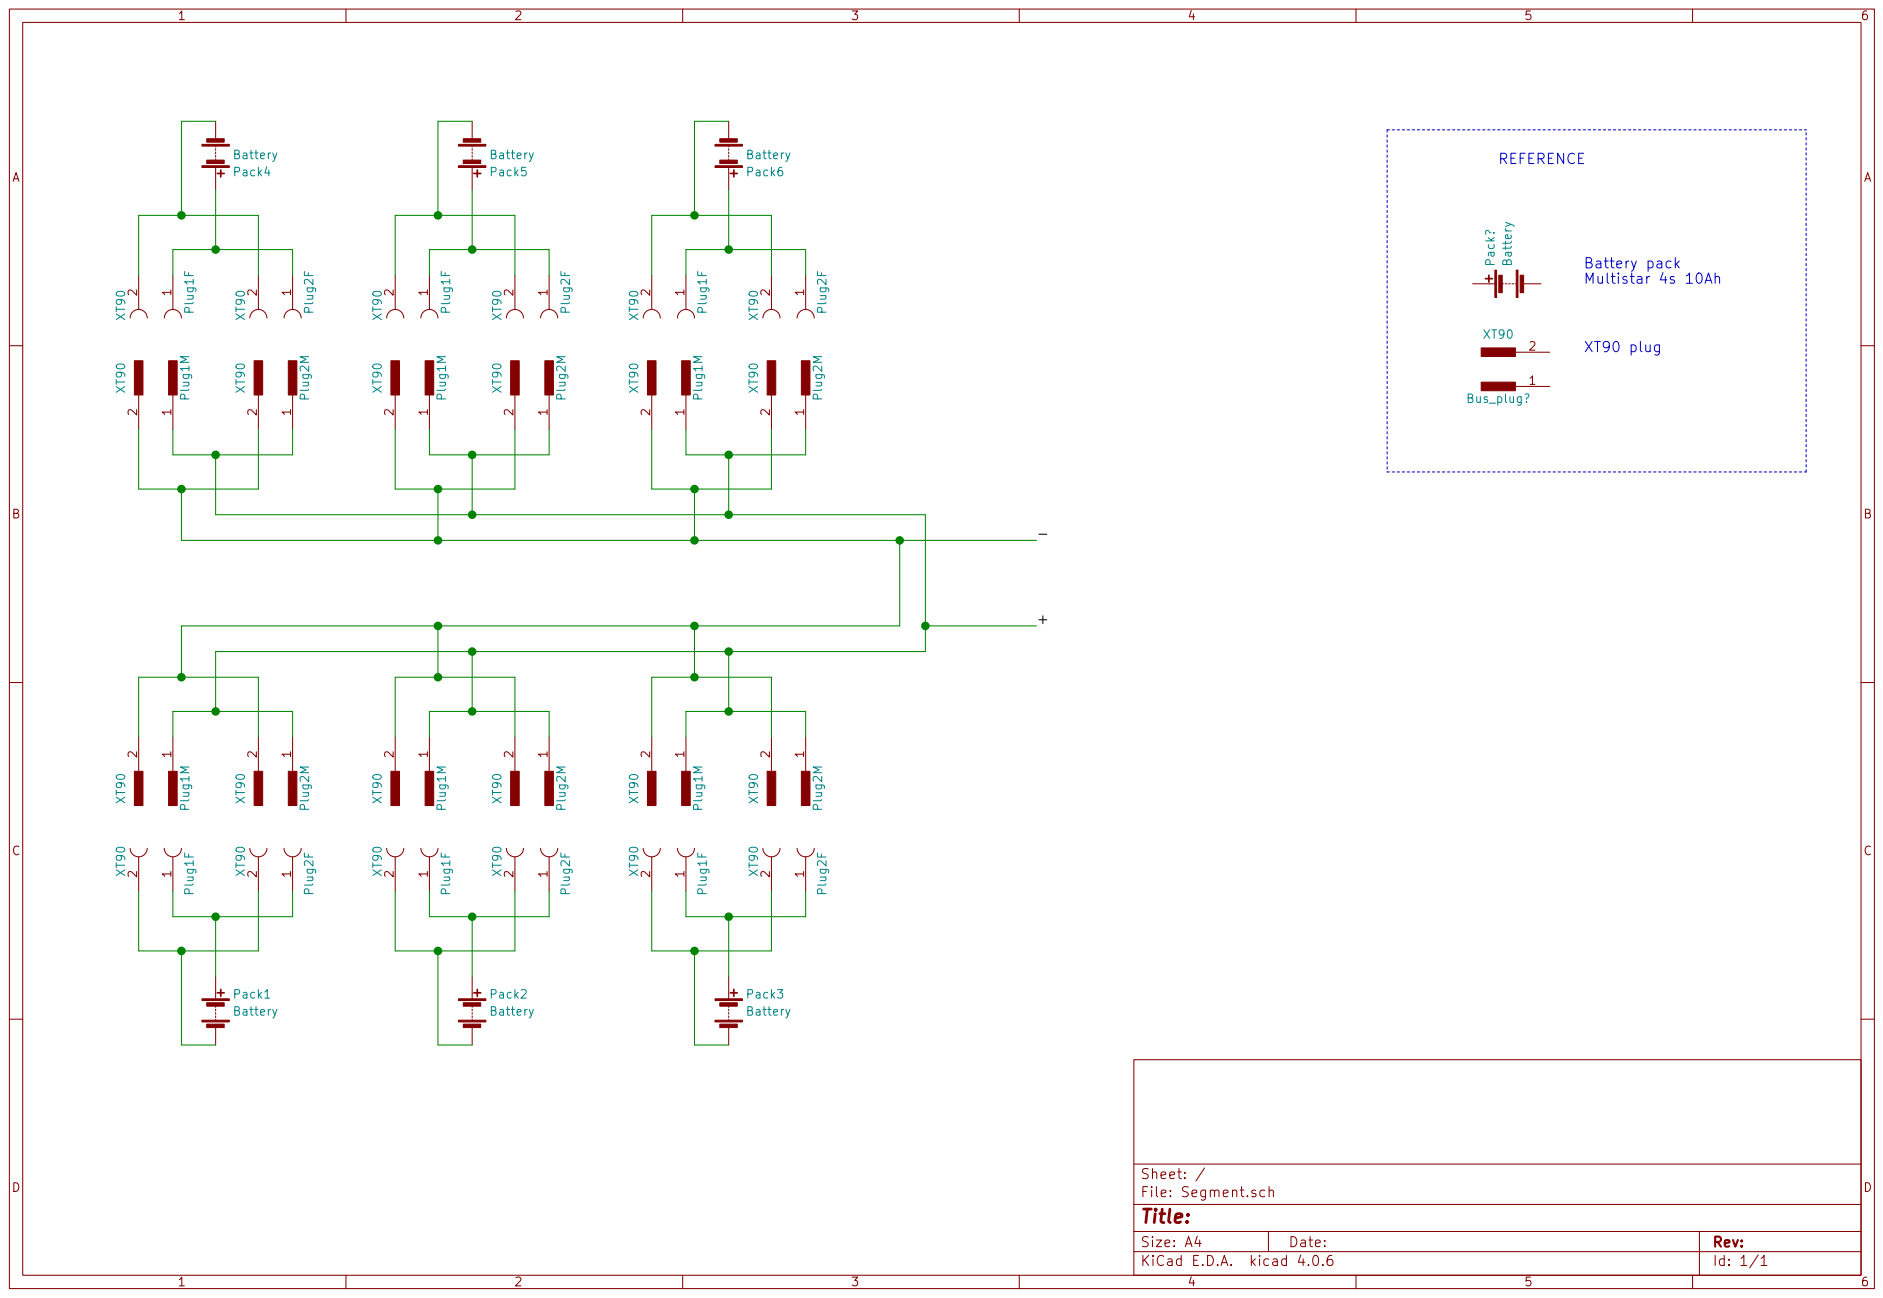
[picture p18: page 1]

Battery pack Multistar 4s 10Ah XT90 plug

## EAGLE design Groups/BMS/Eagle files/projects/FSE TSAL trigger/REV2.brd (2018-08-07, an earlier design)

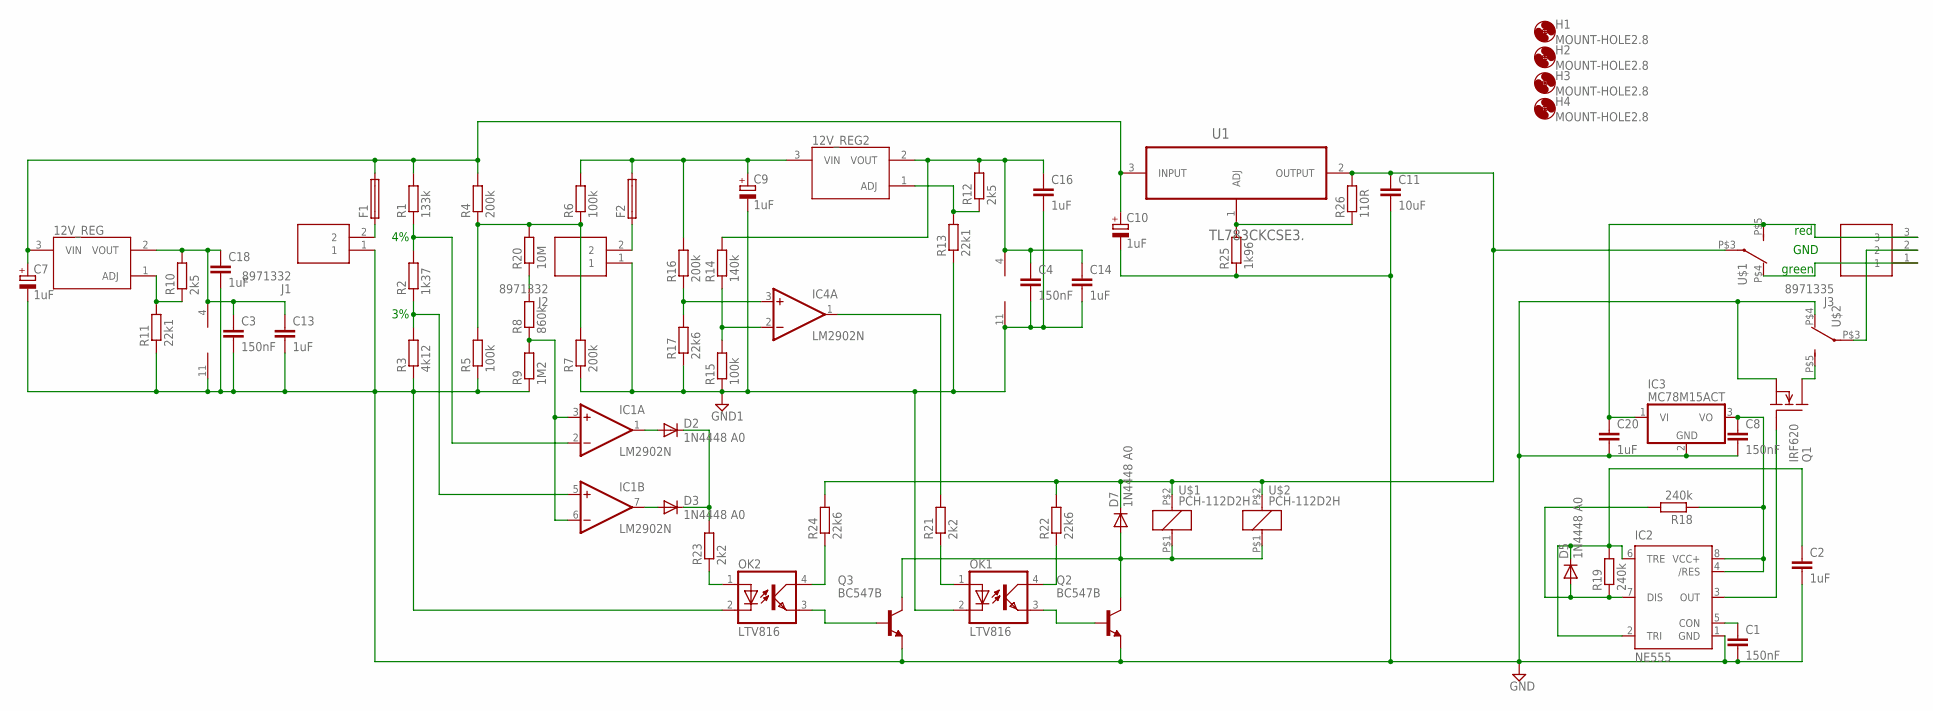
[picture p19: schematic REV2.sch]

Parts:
12V_REG, 12V_REG2: LR8LR8; TO92-LINE
C1, C3, C4, C8: 150nF; C050-024X044
C2, C13, C14, C16, C18, C20: 1uF; C025-030X050
C7, C9, C10: 1uF; E3,5-8
C11: 10uF; C050-075X075
D2, D3, D5, D7: 1N4448 A0; DO35-10
F1, F2: GSH15
H1, H2, H3, H4: MOUNT-HOLE2.8; 2,8
IC1, IC4: LM2902N; DIL14
IC2: NE555; DIL-08
IC3: MC78M15ACT; TO220V
J1, J2: 8971332; SHDR2W90P0X350_1X2_700X700X850
J3: 8971335; SHDR3W90P0X350_1X3_1050X700X85
OK1, OK2: LTV816; DIL04
Q1: IRF620; TO220
Q2, Q3: BC547B; TO92
R1: 133k; 0207/10
R2: 1k37; 0207/10
R3: 4k12; 0207/10
R4, R7, R16: 200k; 0207/10
R5, R6, R15: 100k; 0207/10
R8: 860k; 0207/10
R9: 1M2; 0207/10
R10, R12: 2k5; 0207/10
R11, R13: 22k1; 0207/10
R14: 140k; 0207/10
R17, R22, R24: 22k6; 0207/10
R18, R19: 240k; 0207/10
R20: 10M; 0207/10
R21, R23: 2k2; 0207/10
R25: 1k96; 0309/10
R26: 110R; 0309/10
U1: TL783CKCSE3.; TO254P457X1016X2222-3P
U$1, U$2: PCH-112D2H

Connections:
GND: C1.2, C2.2, C3.2, C7.-, C8.2, C10.-, C11.2, C13.2, C18.2, C20.2, IC1.11 (V-), IC2.1 (GND), IC3.2 (GND), J1.1, OK2.2 (C), Q1.3 (S), Q2.1 (E), Q3.1 (E), R3.1, R5.1, R9.1, R11.1, R25.1, U$2.P$4 (O)
GND1: C4.2, C9.-, C14.2, C16.2, IC4.11 (V-), J2.1, OK1.2 (C), R7.1, R13.1, R15.1, R17.1
unnamed: 12V_REG.3 (VIN), C7.+, C10.+, F1.2, R1.2, R4.2, U1.3 (INPUT)
unnamed: IC1.2 (-IN), R1.1, R2.2
unnamed: IC1.5 (+IN), R2.1, R3.2
unnamed: C11.1, D7.C, R22.2, R24.2, R26.2, U1.2 (OUTPUT), U$1.P$2 (1), U$1.P$3, U$2.P$2 (1)
unnamed: 12V_REG2.3 (VIN), C9.+, F2.2, R6.2, R16.2
unnamed: IC2.3 (OUT), Q1.1 (G)
unnamed: F1.1, J1.2
unnamed: IC4.1 (OUT), R21.2
unnamed: 12V_REG.2 (VOUT), C3.1, C13.1, C18.1, IC1.4 (V+), R10.2
unnamed: 12V_REG.1 (ADJ), R10.1, R11.2
unnamed: D2.A, IC1.1 (OUT)
unnamed: D3.A, IC1.7 (OUT)
unnamed: D2.C, D3.C, R23.2
unnamed: F2.1, J2.2
unnamed: C1.1, IC2.5 (CON)
unnamed: D5.A, IC2.7 (DIS), R18.2, R19.1
unnamed: C20.1, IC3.1 (VI), J3.3, U$1.P$5 (S)
unnamed: C2.1, D5.C, IC2.2 (TRI), IC2.6 (TRE), R19.2
unnamed: C8.1, IC2.4 (/RES), IC2.8 (VCC+), IC3.3 (VO), R18.1
unnamed: IC4.3 (+IN), R16.1, R17.2
unnamed: J3.1, U$1.P$4 (O)
unnamed: 12V_REG2.2 (VOUT), C4.1, C14.1, C16.1, IC4.4 (V+), R12.2, R14.2
unnamed: Q1.2 (D), U$2.P$5 (S)
unnamed: IC4.2 (-IN), R14.1, R15.2
unnamed: 12V_REG2.1 (ADJ), R12.1, R13.2
unnamed: R4.1, R5.2, R6.1, R7.2, R20.2
unnamed: IC1.3 (+IN), IC1.6 (-IN), R8.1, R9.2
unnamed: R8.2, R20.1
unnamed: R25.2, R26.1, U1.1 (ADJ)
unnamed: OK2.1 (A), R23.1
unnamed: OK2.4 (COL), R24.1
unnamed: J3.2, U$2.P$3
unnamed: D7.A, Q2.3 (C), Q3.3 (C), U$1.P$1 (2), U$2.P$1 (2)
unnamed: OK2.3 (EMIT), Q3.2 (B)
unnamed: OK1.1 (A), R21.1
unnamed: OK1.4 (COL), R22.1
unnamed: OK1.3 (EMIT), Q2.2 (B)

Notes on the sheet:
green
red
GND

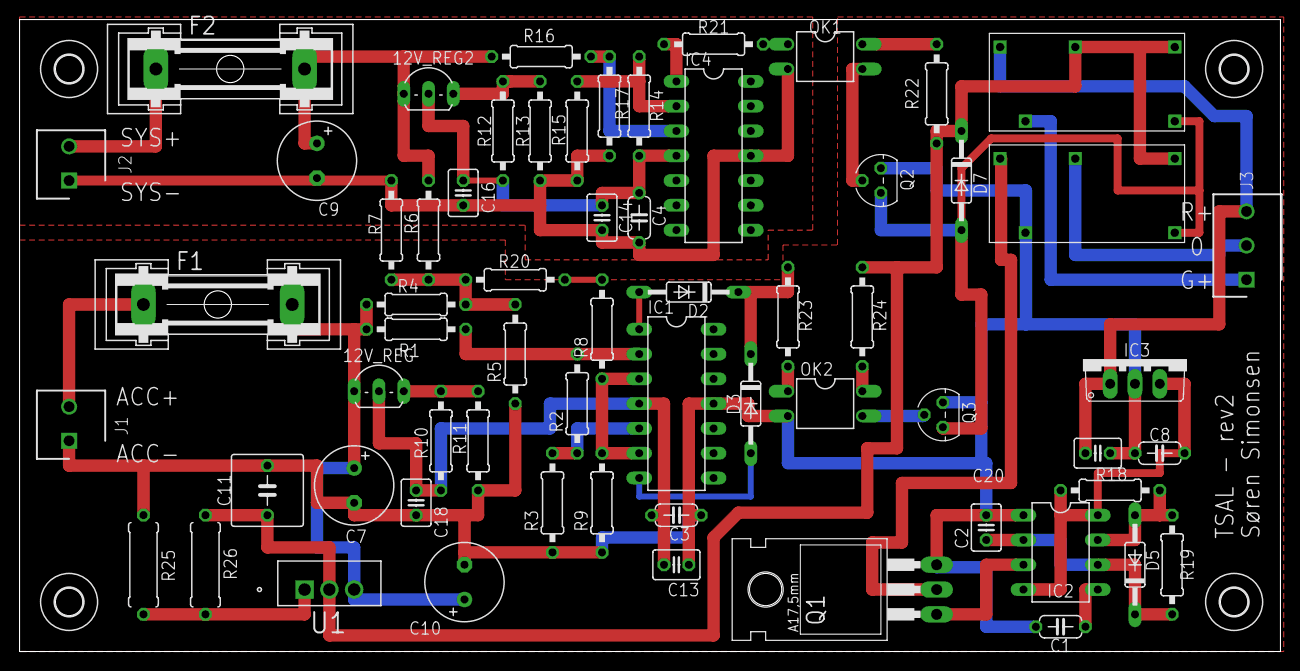
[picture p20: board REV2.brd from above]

Board: 2 copper layers, 129.2 x 64.8 mm, 67 parts (0 on the bottom side), 39 nets.

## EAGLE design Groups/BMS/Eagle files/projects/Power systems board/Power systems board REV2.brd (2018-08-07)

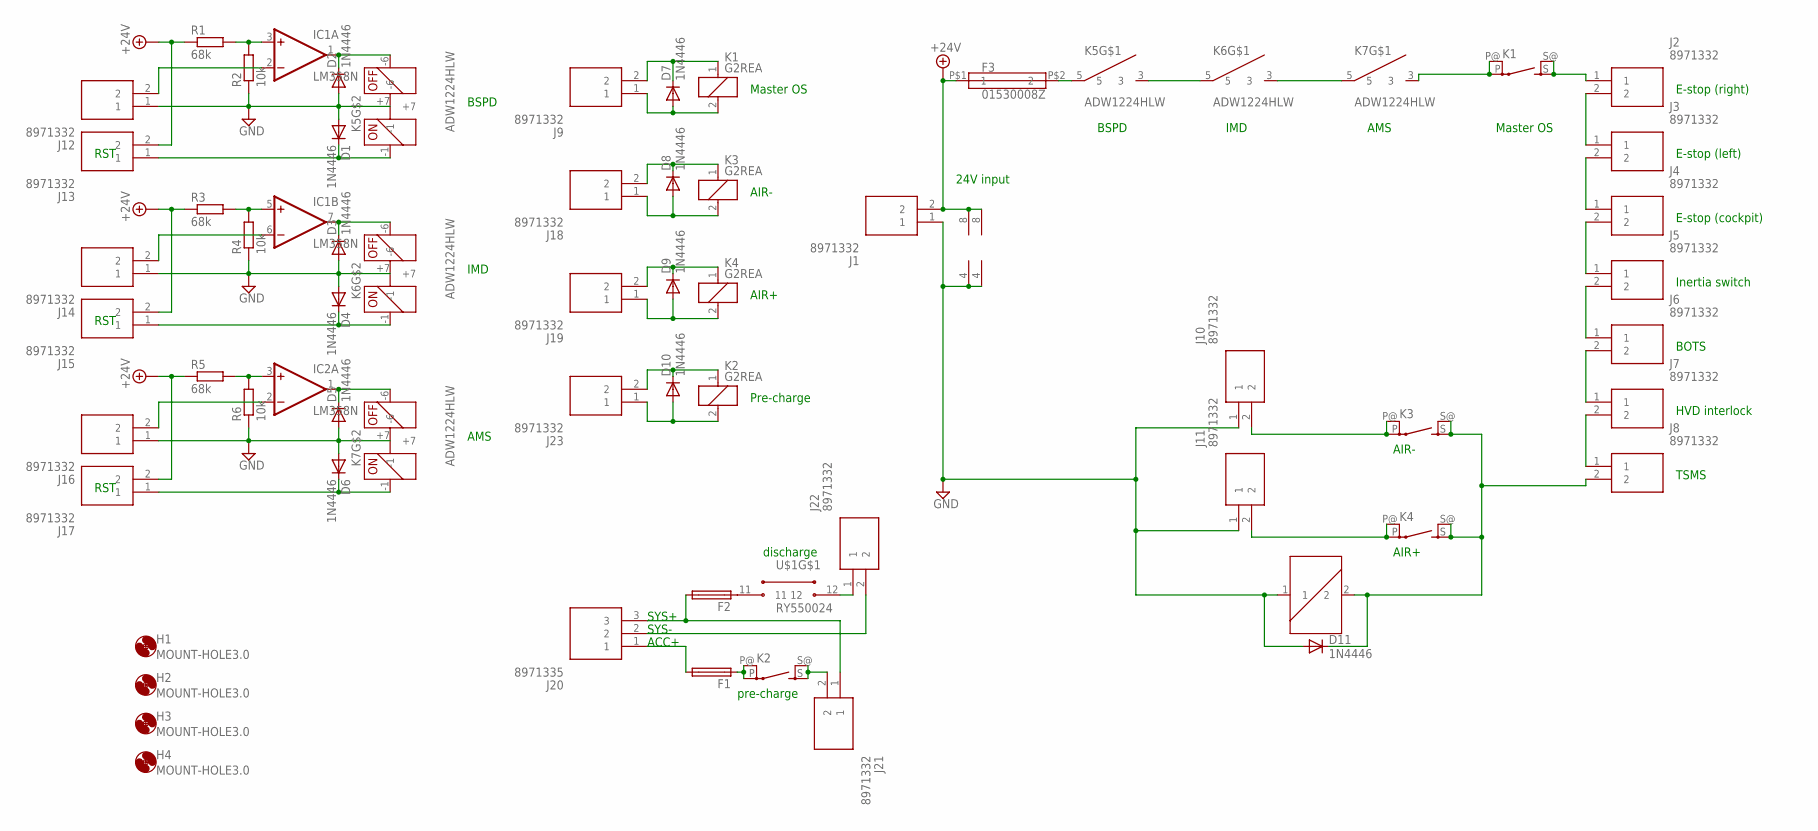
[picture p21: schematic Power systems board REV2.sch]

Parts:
D1, D2, D3, D4, D5, D6, D7, D8, D9, D10, D11: 1N4446; DO35-10
F1, F2: GSH15
F3: 01530008Z
H1, H2, H3, H4: MOUNT-HOLE3.0; 3,0
IC1, IC2: LM358N; DIL08
J1, J2, J3, J4, J5, J6, J7, J8, J9, J10, J11, J12, J13, J14, J15, J16, J17, J18, J19, J21, J22, J23: 8971332; SHDR2W90P0X350_1X2_700X700X850
J20: 8971335; SHDR3W90P0X350_1X3_1050X700X85
K1, K2, K3, K4: G2REA
K5, K6, K7: ADW1224HLW
R1, R3, R5: 68k; 0204/7
R2, R4, R6: 10k; 0204/7
U$1: RY550024

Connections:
+24V: F3.P$1 (1), IC1.8 (V+), IC2.8 (V+), J1.2, J13.2, J15.2, J17.2, R1.1, R3.1, R5.1
GND: D1.A, D2.A, D3.A, D4.A, D5.A, D6.A, D11.A, IC1.4 (V-), IC2.4 (V-), J1.1, J10.1, J11.1, J12.1, J14.1, J16.1, K5.+7, K6.+7, K7.+7, R2.1, R4.1, R6.1, U$1.1
unnamed: IC1.3 (+IN), R1.2, R2.2
unnamed: K5.3, K6.5
unnamed: K6.3, K7.5
unnamed: K1.P, K1.P@, K7.3
unnamed: J2.1, K1.S, K1.S@ (S)
unnamed: J2.2, J3.1
unnamed: J3.2, J4.1
unnamed: J4.2, J5.1
unnamed: J5.2, J6.1
unnamed: J6.2, J7.1
unnamed: J7.2, J8.1
unnamed: D11.C, J8.2, K3.S, K3.S@ (S), K4.S, K4.S@ (S), U$1.2
unnamed: J10.2, K3.P, K3.P@
unnamed: J11.2, K4.P, K4.P@
unnamed: F1.1, K2.P, K2.P@
unnamed: D2.C, IC1.1 (OUT), K5.-6
unnamed: IC1.2 (-IN), J12.2
unnamed: D1.C, J13.1, K5.-1
unnamed: IC1.5 (+IN), R3.2, R4.2
unnamed: IC1.6 (-IN), J14.2
unnamed: D5.C, IC2.1 (OUT), K7.-6
unnamed: D4.C, J15.1, K6.-1
unnamed: D3.C, IC1.7 (OUT), K6.-6
unnamed: D7.C, J9.2, K1.1
unnamed: IC2.2 (-IN), J16.2
unnamed: IC2.3 (+IN), R5.2, R6.2
unnamed: D7.A, J9.1, K1.2
unnamed: D6.C, J17.1, K7.-1
unnamed: D8.C, J18.2, K3.1
unnamed: D8.A, J18.1, K3.2
unnamed: D9.C, J19.2, K4.1
unnamed: D9.A, J19.1, K4.2
unnamed: F1.2, J20.1
unnamed: F2.2, J20.3, J21.1
unnamed: J21.2, K2.S, K2.S@ (S)
unnamed: J20.2, J22.2
unnamed: D10.C, J23.2, K2.1
unnamed: D10.A, J23.1, K2.2
unnamed: F3.P$2 (2), K5.5
unnamed: F2.1, U$1.11
unnamed: J22.1, U$1.12

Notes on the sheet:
24V input
BSPD
IMD
AMS
Master OS
E-stop (right)
E-stop (left)
E-stop (cockpit)
Inertia switch
BOTS
HVD interlock
TSMS
Pre-charge
AIR-
AIR+
RST
SYS+
SYS-
ACC+
pre-charge
discharge

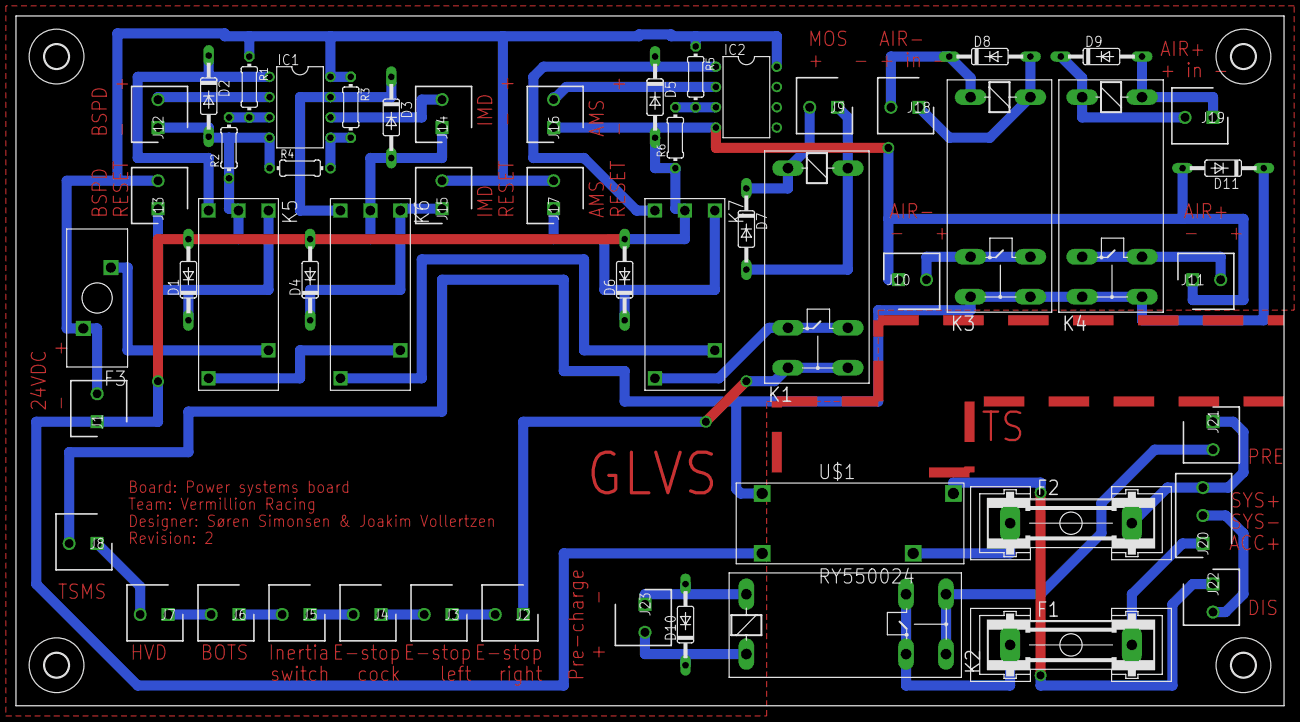
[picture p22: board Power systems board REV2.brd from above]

Board: 2 copper layers, 158.8 x 86.4 mm, 57 parts (0 on the bottom side), 43 nets.

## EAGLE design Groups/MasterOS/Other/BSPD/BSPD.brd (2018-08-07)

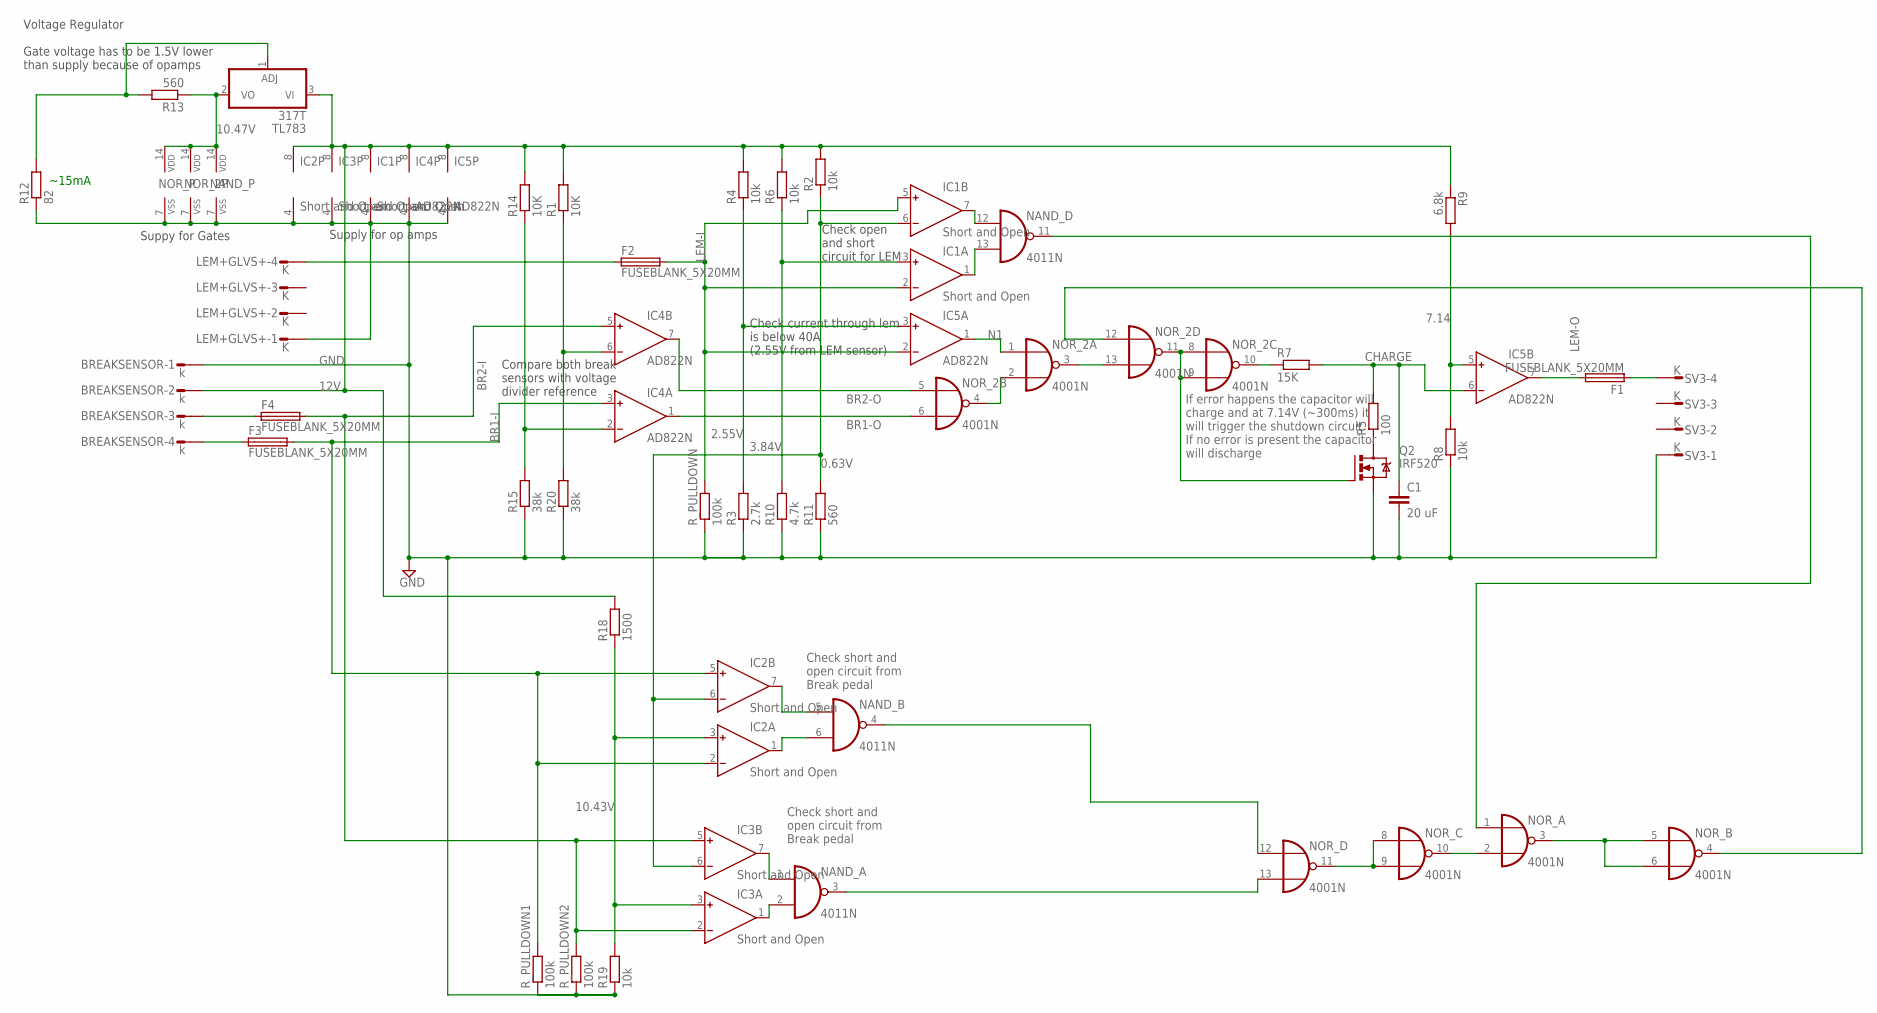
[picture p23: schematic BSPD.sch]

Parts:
BREAKSENSOR: k; L04P
C1: 20 uF; C2.5-5
F1, F2, F3, F4: FUSEBLANK_5X20MM; FUSE_HOLDER_5X20MM
IC1, IC2, IC3: Short and Open; DIL08
IC4, IC5: AD822N; DIL08
LEM+GLVS+: K; L04P
NAND_: 4011N; DIL14
NOR_, NOR_2: 4001N; DIL14
Q2: IRF520; TO220BV
R1, R14: 10K; 0204/7
R2, R4, R6, R8: 10k; 0204/7
R3: 2.7k; 0204/7
R5: 100; 0207/10
R7: 15K; 0207/10
R9: 6.8k; 0204/7
R10: 4.7k; 0204/7
R11, R13: 560; 0204/7
R12: 82; 0204/7
R15, R20: 38k; 0207/10
R18: 1500; 0207/10
R19: 10k; 0207/10
R_PULLDOWN, R_PULLDOWN1, R_PULLDOWN2: 100k; 0204/7
SV3: K; L04P
TL783: 317T; TO220H

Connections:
0.63V: IC1.6 (IN-), IC2.6 (IN-), IC3.6 (IN-), R2.1, R11.2
2.55V: IC5.3 (IN+), R3.2, R4.1
3.84V: IC1.3 (IN+), R6.1, R10.2
7.14: IC5.5 (IN+), R8.2, R9.2
10.43V: IC2.3 (IN+), IC3.3 (IN+), R18.1, R19.2
10.47V: NAND_.14 (VDD), NOR_.14 (VDD), NOR_2.14 (VDD), R13.1, TL783.2 (VO)
12V: BREAKSENSOR.2, IC1.8 (V+), IC2.8 (V+), IC3.8 (V+), IC4.8 (V+), IC5.8 (V+), R1.2, R2.2, R4.2, R6.2, R9.1, R14.2, R18.2, TL783.3 (VI)
BR1-I: F3.2, IC2.2 (IN-), IC2.5 (IN+), IC4.3 (IN+), R_PULLDOWN1.2
BR1-O: IC4.1 (OUT), NOR_2.6 (I1)
BR2-I: F4.2, IC3.2 (IN-), IC3.5 (IN+), IC4.5 (IN+), R_PULLDOWN2.2
BR2-O: IC4.7 (OUT), NOR_2.5 (I0)
CHARGE: C1.1, IC5.6 (IN-), R5.2, R7.2
GND: BREAKSENSOR.1, C1.2, IC1.4 (V-), IC2.4 (V-), IC3.4 (V-), IC4.4 (V-), IC5.4 (V-), LEM+GLVS+.1, NAND_.7 (VSS), NOR_.7 (VSS), NOR_2.7 (VSS), Q2.S, R3.1, R8.1, R10.1, R11.1, R12.1, R15.1, R19.1, R20.1, R_PULLDOWN.1, R_PULLDOWN1.1, R_PULLDOWN2.1, SV3.1
LEM-I: F2.2, IC1.2 (IN-), IC1.5 (IN+), IC5.2 (IN-), R_PULLDOWN.2
LEM-O: F1.2, IC5.7 (OUT)
N1: IC5.1 (OUT), NOR_2.1 (I0)
unnamed: NOR_2.3 (O), NOR_2.13 (I1)
unnamed: IC4.2 (IN-), R14.1, R15.2
unnamed: NOR_2.2 (I1), NOR_2.4 (O)
unnamed: R12.2, R13.2, TL783.1 (ADJ)
unnamed: NOR_2.8 (I0), NOR_2.9 (I1), NOR_2.11 (O), Q2.G
unnamed: NOR_.8 (I0), NOR_.9 (I1), NOR_.11 (O)
unnamed: NAND_.3 (O), NOR_.13 (I1)
unnamed: NOR_.4 (O), NOR_2.12 (I0)
unnamed: NOR_.2 (I1), NOR_.10 (O)
unnamed: IC1.1 (OUT), NAND_.13 (I1)
unnamed: Q2.D, R5.1
unnamed: F1.1, SV3.4
unnamed: F2.1, LEM+GLVS+.4
unnamed: IC1.7 (OUT), NAND_.12 (I0)
unnamed: NAND_.4 (O), NOR_.12 (I0)
unnamed: IC2.1 (OUT), NAND_.6 (I1)
unnamed: IC2.7 (OUT), NAND_.5 (I0)
unnamed: IC3.1 (OUT), NAND_.2 (I1)
unnamed: IC3.7 (OUT), NAND_.1 (I0)
unnamed: NAND_.11 (O), NOR_.1 (I0)
unnamed: BREAKSENSOR.4, F3.1
unnamed: NOR_.3 (O), NOR_.5 (I0), NOR_.6 (I1)
unnamed: NOR_2.10 (O), R7.1
unnamed: BREAKSENSOR.3, F4.1
NS$3: IC4.6 (IN-), R1.1, R20.2

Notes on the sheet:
~15mA
Voltage Regulator Gate voltage has to be 1.5V lower than supply because of opamps
Suppy for Gates
Supply for op amps
Compare both break sensors with voltage divider reference
Check open and short circuit for LEM
Check current through lem is below 40A (2.55V from LEM sensor)
Check short and open circuit from Break pedal
If error happens the capacitor will charge and at 7.14V (~300ms) it will trigger the shutdown circuit If no error is present the capacitor will discharge

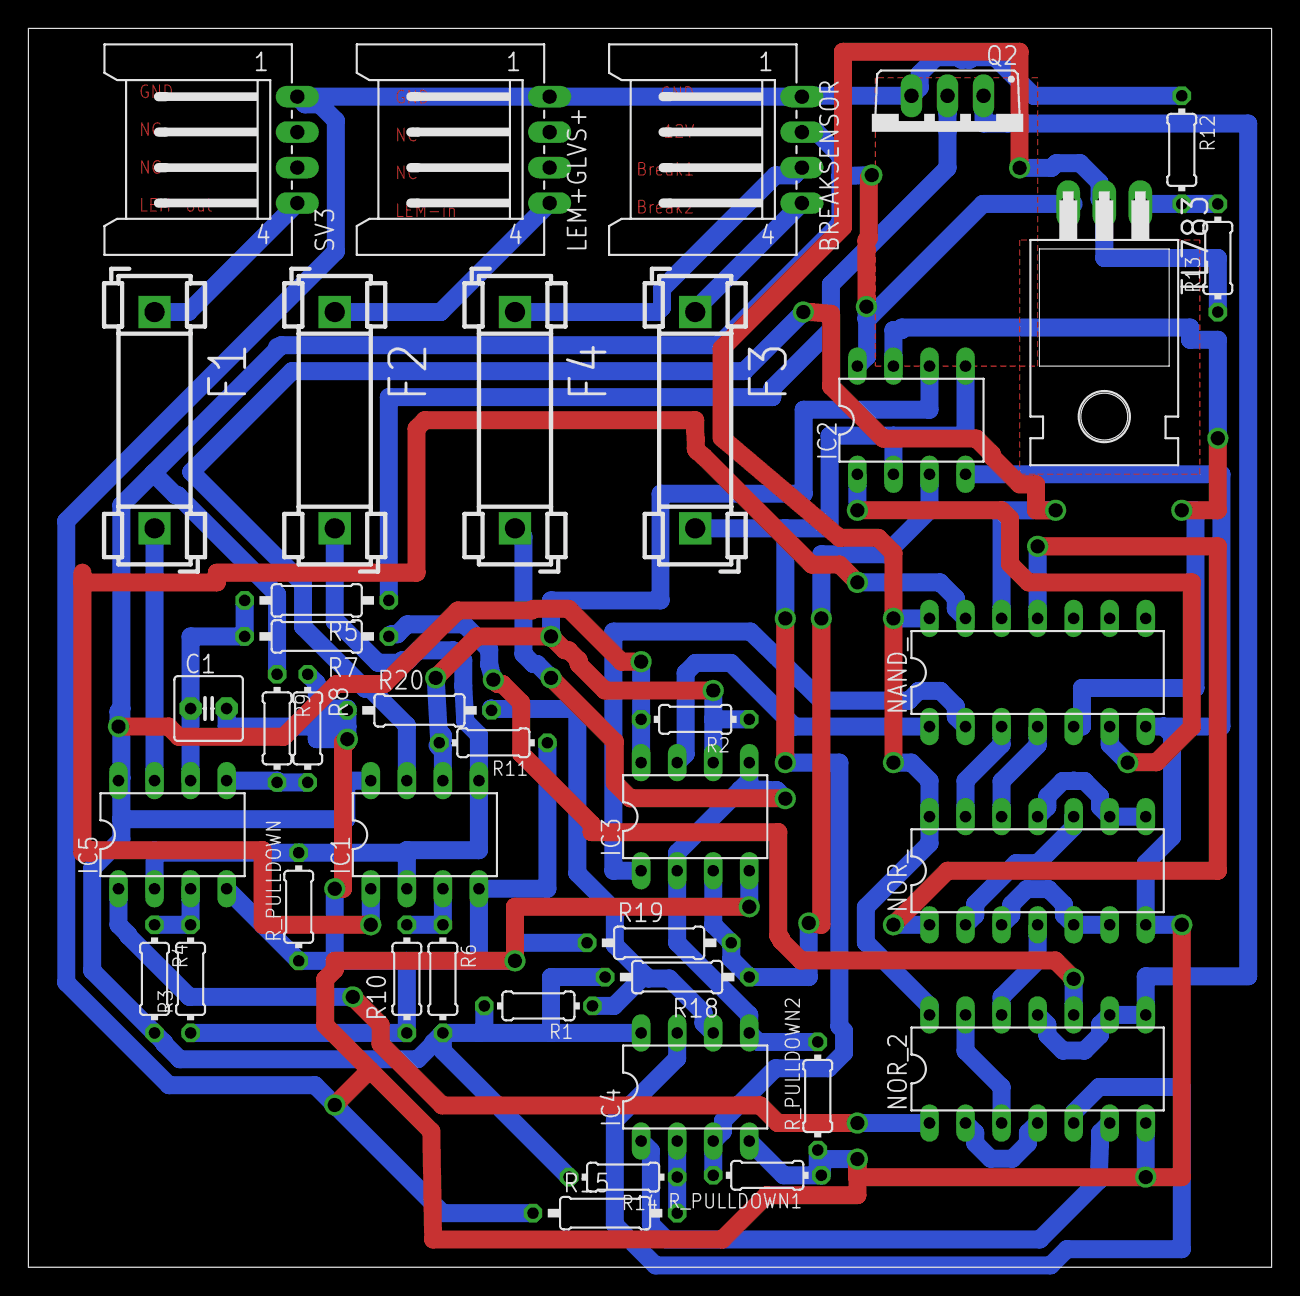
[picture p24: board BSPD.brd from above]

Board: 2 copper layers, 87.6 x 87.3 mm, 39 parts (0 on the bottom side), 41 nets.

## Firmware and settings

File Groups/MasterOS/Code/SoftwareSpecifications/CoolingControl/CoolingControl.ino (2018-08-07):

/*
 * Items: Cooling Control
 * Description: CAN interface for cooling pump control.
 * Original author: Frederik Krogsdal Jacobsen <s163949@student.dtu.dk>
 * 
 * CAN packets:
 *    Sends:
 *      Normal operation on ID 710
 *      Error on ID 90
 *    Receives:
 *      Motor Status from ID 720
 *      
 * Electrical connections:
 *  Must run on an Arduino Uno R3 with a Arduino Uno click shield (MIKROE-1581).
 *  The click shield must contain a CAN SPI click board (MIKROE-986) in slot 1.
 *  Additionally, the following connections must be made in slot 2 of the click
 *  shield:
 *    Cooling Pump Signal 1 must be connected to analog pin 3
 *    Cooling Pump Signal 2 must be connected to analog pin 5
 *    
 *  An error LED can optionally be connected to analog pin 5.
 *  A serial read-out of the current state is available on the USB interface of 
 *  the Arduino.
 * 
 * Functional specification:
 *  The interface controls the two pumps for the watercooling system.
 *  If the serial or CAN interface can not be initialized, the error LED is lit,
 *  and both Cooling Pump Signal 1 and Cooling Pump Signal 2 are held at a duty
 *  cycle of 100% until the interface is rebooted.
 *  
 *  The interface controls the pumps using a state machine with three states.
 *  The states are called MOTOR_ON, MOTOR_OFF_LOW_T, and MOTOR_OFF_HIGH_T.
 *  In the MOTOR_ON state, both Cooling Pump Signal 1 and Cooling Pump Signal 2
 *  are held at a duty cycle of 100% regardless of the motor temperature.
 *  In the MOTOR_OFF_LOW_T state, both Cooling Pump Signal 1 and
 *  Cooling Pump Signal 2 are held at a duty cycle of 0%.
 *  In the MOTOR_OFF_HIGH_T state, both Cooling Pump Signal 1 and
 *  Cooling Pump Signal 2 are held at a duty cycle of 100%.
 *  When the interface receives a CAN packet with ID 720 (a Motor Status packet
 *  from the Master Controller), the interface updates the values of the
 *  motor power and motor temperature.
 *  If the motor power is above 5 kW, the state machine transitions to the
 *  MOTOR_ON state.
 *  If the motor power is not above 5 kW, and the state machine is currently
 *  in the MOTOR_OFF_LOW_T state, the interface checks whether the motor
 *  temperature is above 60 degrees Celsius.
 *  If the motor temperature is above 60 degrees Celsius, the state machine
 *  transitions to the MOTOR_OFF_HIGH_T state, otherwise it remains in the
 *  MOTOR_OFF_LOW_T state.
 *  If the motor power is not above 5 kW, and the state machine is currently
 *  int the MOTOR_OFF_HIGH_T state, the interface checks whether the motor
 *  temperature is below 50 degrees Celsius.
 *  If the motor temperature is below 50 degrees Celsius, the state machine
 *  transitions to the MOTOR_OFF_LOW_T state, otherwise it remains in the
 *  MOTOR_OFF_HIGH_T state.
 *  Note that the state machine has some hysteresis in its transitions between
 *  the MOTOR_OFF_LOW_T state and the MOTOR_OFF_HIGH_T state.
 *  
 *  Whenever the state machine transitions to a new state, the interface sends
 *  a CAN packet on ID 710 containing the new value of Cooling Pump Signal 1.
 *  NOTE: THIS FUNCTIONALITY IS NOT YET IMPLEMENTED.
 *  
 *  If the interface does not receive any CAN traffic with ID 720 for more
 *  than 1 second, it assumes a connection failure and transitions the state
 *  machine to the MOTOR_ON state.
 *  NOTE: THIS FUNCTIONALITY IS NOT YET IMPLEMENTED.
 * 
 * Libraries:
 *  The interface requires a library for interfacing with the MCP2515 chip
 *  used for CAN communications.
 *  The standard Arduino CAN library is NOT compatible with the MIKROE-986,
 *  so a modified version of the library must be used.
 */
#include <Arduino.h>
#include <CAN.h>
#include "CoolingControl.h"

/*
 * Global variables
 */
can_data_t canData;
unsigned long timeoutTime;


/*
 * State machine
 */
state_t run_state(state_t cur_state, instance_data_t *data) {
  return state_table[cur_state](data);
};

state_t cur_state;
 
state_t do_state_motor_on(instance_data_t *data) {
  if (data->motorPower > MIN_POWER) {
    return MOTOR_ON;
  } else {
    if (data->motorTemp > NORMAL_TEMP) {
      return MOTOR_OFF_HIGH_T;
    } else {
      return MOTOR_OFF_LOW_T;
    }
  }
}

state_t do_state_motor_off_low_t(instance_data_t *data) {
  if (data->motorPower > MIN_POWER) {
    return MOTOR_ON;
  } else {
    if (data->motorTemp > (NORMAL_TEMP + HYSTERESIS)) {
      return MOTOR_OFF_HIGH_T;
    } else {
      return MOTOR_OFF_LOW_T;
    }
  }
}

state_t do_state_motor_off_high_t(instance_data_t *data) {
  if (data->motorPower > MIN_POWER) {
    return MOTOR_ON;
  } else {
    if (data->motorTemp < (NORMAL_TEMP - HYSTERESIS)) {
      return MOTOR_OFF_LOW_T;
    } else {
      return MOTOR_OFF_HIGH_T;
    }
  }
}

void setup(void) {
  Serial.begin(115200);
  while(!Serial);
  Serial.println("Cooling Control CAN Interface");

  pinMode(PUMP_PIN1, OUTPUT);
  pinMode(PUMP_PIN2, OUTPUT);
  pinMode(ERROR_PIN, OUTPUT);

  CAN.onReceive(onReceive);

  if (!CAN.begin(1000E3)) {
    Serial.println("CAN startup failed!");
    Serial.println("Turning off cooling system forever.");
    Serial.println("Reboot to resume normal operation.");
    analogWrite(PUMP_PIN1, 0);
    analogWrite(PUMP_PIN2, 0);
    digitalWrite(ERROR_PIN, 1);
    while(1);
  }

  CAN.filter(CAN_ID_MOTOR_STATUS);

  analogWrite(PUMP_PIN1, 0);
  analogWrite(PUMP_PIN2, 0);
  digitalWrite(ERROR_PIN, 0);
  
  cur_state = MOTOR_OFF_LOW_T;

  Serial.println("Setup complete - beginning normal operation.");
}

void loop(void) { 
  instance_data_t data = {0};
  data.motorPower = canData.data[0];
  data.motorTemp = canData.data[1];

  cur_state = run_state(cur_state, &data);

  if (millis() - timeoutTime >= TIMEOUT_PERIOD) {
    cur_state = MOTOR_ON;
  }

  switch (cur_state) {
    case MOTOR_ON:
    case MOTOR_OFF_HIGH_T:
      data.pumpControl = 100;
      break;
    case MOTOR_OFF_LOW_T:
      data.pumpControl = 0;
      break;
    default:
      digitalWrite(ERROR_PIN, 1);
      analogWrite(PUMP_PIN1, 0);
      analogWrite(PUMP_PIN2, 0);
      while (100) {
        Serial.println("State machine failure!!! -- reverting to motor off - low temperature state");
      }
      cur_state = MOTOR_OFF_LOW_T;
  }

  analogWrite(PUMP_PIN1, (data.pumpControl / 100) * ANALOG_STEPS);
  analogWrite(PUMP_PIN2, (data.pumpControl / 100) * ANALOG_STEPS);

  Serial.print("Current state: ");
  Serial.println(cur_state);
}

void onReceive(int packetSize) {
  canData.id = CAN.packetId();
  if (canData.id == 720) {
    timeoutTime = millis();
  }
  
  for(int i = 0; i < 8; i++) {
    canData.data[i] = CAN.read();
  }
}

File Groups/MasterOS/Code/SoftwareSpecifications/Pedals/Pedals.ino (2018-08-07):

#include <EEPROM.h>
#include <CAN.h>

//pins
#define BRAKE_1 A1
#define BRAKE_2 A2
#define ACC_1 A4
#define ACC_2 A5
#define STEERING A0
#define STATUS_LED 3
#define BTN 5

//constants
#define TOLERANCE 20
#define MISMATCH 40
#define CONNECTION_BREAK 1000
#define CONNECTION_SHORT 23
#define FLASH_SPEED 100
#define CALIBRATION_TOLERANCE 10
#define SAMPLES 20
#define MISSMATCH_DELAY

// ID of the settings block
#define CONFIG_VERSION "ls3"

// config address in eeprom
#define CONFIG_START 32

struct StoreStruct {
  char dataVersion[4];
  int sensorConfig[5][2];
} storage = {
  // The default values
  CONFIG_VERSION,
  {{255, 767}, {255, 767}, {255, 767}, {225, 767}, {20, 1003}}
};

byte brake = 0;
byte apps = 0;
int steering = 0;
int error = 0;
int configAdress = 0;
bool pressed = true;

unsigned long brakeMissMatch = 0;
unsigned long appsMissMatch = 0;
unsigned long currentMillis = 0;

void setup() {
  //setup GPIOs
  pinMode(BTN, INPUT_PULLUP);
  pinMode(STATUS_LED, OUTPUT);
  digitalWrite(STATUS_LED, LOW);

  //Serial.begin(9600);
  //while (!Serial);
  //Serial.println("CAN Sender");
  // start the CAN bus at 500 kbps 
  if (!CAN.begin(1000E3)) {
    //Serial.println("Starting CAN failed!");
    while (1);
  }

  loadConfig();
}

void loop() {
  //check if button is pushed once
  if (!pressed && !digitalRead(BTN)) {
    calibrate();
    pressed = true;
  } else if (digitalRead(BTN)) {
    pressed = false;
  }

  getInput();
  if (error) {
    CAN.beginPacket(10);
    CAN.write(error>>8);
    CAN.write(error);
    CAN.endPacket();
  }

  
  CAN.beginPacket(110);
  CAN.write(brake);
  CAN.write(apps);
  CAN.write(steering>>8);
  CAN.write(steering);
  CAN.endPacket();
  
  //  Serial.print(analogRead(ACC_1));
  //  Serial.print("\t");
  //  Serial.println(storage.sensorConfig[0][0]);

  //  Serial.println("error, brake, apps, steering");
  //  Serial.println(error, BIN);
  //  Serial.println(brake);
  //  Serial.println(apps);
  //  Serial.println(steering);


  delay(50);
}

void loadConfig() {
  // If nothing is found it will use the default settings.
  if (EEPROM.read(CONFIG_START + 0) == CONFIG_VERSION[0] &&
      EEPROM.read(CONFIG_START + 1) == CONFIG_VERSION[1] &&
      EEPROM.read(CONFIG_START + 2) == CONFIG_VERSION[2])
    for (unsigned int t = 0; t < sizeof(storage); t++)
      *((char*)&storage + t) = EEPROM.read(CONFIG_START + t);
}

void saveConfig() {
  for (unsigned int t = 0; t < sizeof(storage); t++)
    EEPROM.write(CONFIG_START + t, *((char*)&storage + t));
}

void getInput() {

  int acc1 = analogRead(ACC_1);
  int acc2 = analogRead(ACC_2);
  int brake1 = analogRead(BRAKE_1);
  int brake2 = analogRead(BRAKE_2);
  int steeringIn = analogRead(STEERING);

  //detect error
  currentMillis = millis();
  error = 0;

  //mismatch error
  if (abs(brake1 - brake2) < MISMATCH) {
    brakeMissMatch = MISSMATCH_DELAY + currentMillis;
  } else if (brakeMissMatch < currentMillis) {
    error |= 0x01;
  }

  if (abs(acc1 - acc2) < MISMATCH) {
    appsMissMatch = MISSMATCH_DELAY + currentMillis;
  } else if (appsMissMatch < currentMillis) {
    error |= 0x02;
  }

  //brake position error
  if (brake1 > CONNECTION_BREAK || brake2 > CONNECTION_BREAK) {
    error |= 0x40;
  } else if (brake1 > storage.sensorConfig[2][1] + TOLERANCE || brake2 > storage.sensorConfig[3][1] + TOLERANCE) {
    error |= 0x04;
  }
  if (brake1 + TOLERANCE < CONNECTION_SHORT || brake2 + TOLERANCE < CONNECTION_SHORT) {
    error |= 0x0100;
  } else if (brake1 + TOLERANCE < storage.sensorConfig[2][0] || brake2 + TOLERANCE < storage.sensorConfig[3][0]) {
    error |= 0x08;
  }

  //accelerator position error
  if (acc1 > CONNECTION_BREAK || acc2 > CONNECTION_BREAK) {
    error |= 0x80;
  } else if (acc1 > storage.sensorConfig[0][1] + TOLERANCE || acc2 > storage.sensorConfig[1][1] + TOLERANCE) {
    error |= 0x10;
  }
  if (acc1 + TOLERANCE < CONNECTION_SHORT || acc2 + TOLERANCE < CONNECTION_SHORT) {
    error |= 0x0200;
  } else if (acc1 + TOLERANCE < storage.sensorConfig[0][0] || acc2 + TOLERANCE < storage.sensorConfig[1][0]) {
    error |= 0x20;
  }

  //steering position error
  if (steeringIn > CONNECTION_BREAK){
    error |= 0x0400;
  }else if(steeringIn > storage.sensorConfig[4][1]){
    error |= 0x0800;
  }else if (steeringIn < CONNECTION_SHORT){
    error |= 0x1000;
  }else if (steeringIn < storage.sensorConfig[4][0]){
    error |= 0x2000;
  }

  int accLowLimit = storage.sensorConfig[0][0] + storage.sensorConfig[1][0] + TOLERANCE;
  int accUpLimit = storage.sensorConfig[0][1] + storage.sensorConfig[1][1] - TOLERANCE;

  int brakeLowLimit = storage.sensorConfig[2, 0] + storage.sensorConfig[3][0] + TOLERANCE;
  int brakeUpLimit = storage.sensorConfig[2, 1] + storage.sensorConfig[3][1] - TOLERANCE;

  apps = map(constrain(acc1 + acc2, accLowLimit, accUpLimit), accLowLimit, accUpLimit, 0, 255);
  brake = map(constrain(brake1 + brake2, brakeLowLimit, brakeUpLimit), brakeLowLimit, brakeUpLimit, 0, 255);
  steering = constrain(steeringIn, storage.sensorConfig[4][0], storage.sensorConfig[4][1]);

}

void calibrate() {
  struct StoreStruct calibration = storage;

  delay(1000);
  calibration.sensorConfig[0][0] = calibrate(ACC_1);
  calibration.sensorConfig[1][0] = calibrate(ACC_2);
  calibration.sensorConfig[2][0] = calibrate(BRAKE_1);
  calibration.sensorConfig[3][0] = calibrate(BRAKE_2);
  flash(1);
  delay(2000);
  calibration.sensorConfig[0][1] = calibrate(ACC_1);
  calibration.sensorConfig[1][1] = calibrate(ACC_2);
  flash(2);
  delay(2000);
  calibration.sensorConfig[2][1] = calibrate(BRAKE_1);
  calibration.sensorConfig[3][1] = calibrate(BRAKE_2);
  flash(3);
  delay(2000);

  if ( abs(calibration.sensorConfig[0][0] - analogRead(ACC_1)) < CALIBRATION_TOLERANCE &&
       abs(calibration.sensorConfig[1][0] - analogRead(ACC_2)) < CALIBRATION_TOLERANCE &&
       abs(calibration.sensorConfig[2][0] - analogRead(BRAKE_1)) < CALIBRATION_TOLERANCE &&
       abs(calibration.sensorConfig[3][0] - analogRead(BRAKE_2)) < CALIBRATION_TOLERANCE &&
       //Accelerator
       calibration.sensorConfig[0][0] + 100 < calibration.sensorConfig[0][1] &&
       calibration.sensorConfig[1][0] + 100 < calibration.sensorConfig[1][1] &&
       //Brake
       calibration.sensorConfig[0][0] + 100 < calibration.sensorConfig[0][1] &&
       calibration.sensorConfig[1][0] + 100 < calibration.sensorConfig[1][1]) {

    storage = calibration;
    saveConfig();
    flash(4);
  } else {
    digitalWrite(STATUS_LED, HIGH);
  }
}

void flash(int i) { //flash LED i times
  for (i; i > 0; i--) {
    digitalWrite(STATUS_LED, HIGH);
    delay(FLASH_SPEED);
    digitalWrite(STATUS_LED, LOW);
    delay(FLASH_SPEED);
  }
}

int calibrate(int pin) {
  int cal = 0;
  for (int i = 0; i < SAMPLES; i++) {
    cal += analogRead(pin);
  }
  cal /= SAMPLES;
  return cal;
}

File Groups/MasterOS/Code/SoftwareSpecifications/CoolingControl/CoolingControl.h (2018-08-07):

#ifndef _COOLINGCONTROL_H
#define _COOLINGCONTROL_H

/*
 * Global configuration parameters
 */
const int PUMP_PIN1 = 3;
const int PUMP_PIN2 = 5;
const int ERROR_PIN = A5;
const int CAN_ID_MOTOR_STATUS = 720;

const int NORMAL_TEMP = 55; // degree C
const int MIN_POWER = 5; // kW
const int HYSTERESIS = 5; // degree C
const int ANALOG_STEPS = 255;
const unsigned long TIMEOUT_PERIOD = 1000; // milliseconds

/*
 * Data structures
 */
typedef struct {
  long id;
  int data[8];
} can_data_t;
 
 typedef struct {
  int motorPower;  // kW
  int motorTemp;   // degree C
  int pumpControl; // %
} instance_data_t;

/*
 * State machine
 */
typedef enum {MOTOR_ON, MOTOR_OFF_LOW_T, MOTOR_OFF_HIGH_T, NUM_STATES} state_t;
typedef state_t state_func_t(instance_data_t *data);

state_t do_state_motor_on(instance_data_t *data);
state_t do_state_motor_off_low_t(instance_data_t *data);
state_t do_state_motor_off_high_t(instance_data_t *data);

state_func_t* const state_table[NUM_STATES] = {
  do_state_motor_on, do_state_motor_off_low_t, do_state_motor_off_high_t
};

/*
 * Interrupts
 */
void onReceive(int packetSize);

#endif

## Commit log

2018-08-07 Documentation collected
    [133_Class_1_Technical_University_of_Denmark_DS_Rev_1.xls, 133_Class_1_Technical_University_of_Denmark_FMEA_EV_Rev_5.xls, BSPD.brd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]
2018-08-29 Added Torque Vectoring work done in LabView, done by Dominik.
